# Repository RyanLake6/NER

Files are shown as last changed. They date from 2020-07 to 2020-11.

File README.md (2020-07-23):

View this project on [CADLAB.io](https://cadlab.io/project/23021). 

# NER
This is the GitHub repo for all code and schematics created for Northeastern's Electric Racing club.

- Electrical-Arduino: Arduino code for electrical subsystems, mainly the CAN Network
- Project Manangement: Javascript (Google Apps Script) code for various project management backend systems

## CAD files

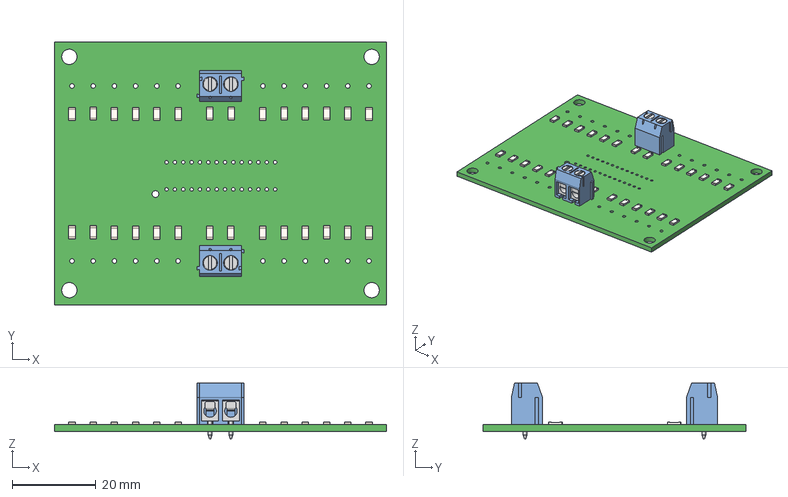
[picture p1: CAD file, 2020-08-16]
Schematics/Battery Managment/Therm_PCB/Therms.step
79.5 x 63.0 x 13.4 mm

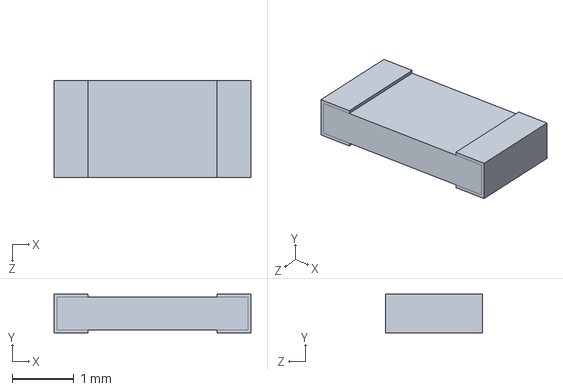
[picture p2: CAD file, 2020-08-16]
Schematics/Battery Managment/VoltTap_PCB/C1T5_CAD_Model.SLDPRT
3.20 x 0.63 x 1.58 mm

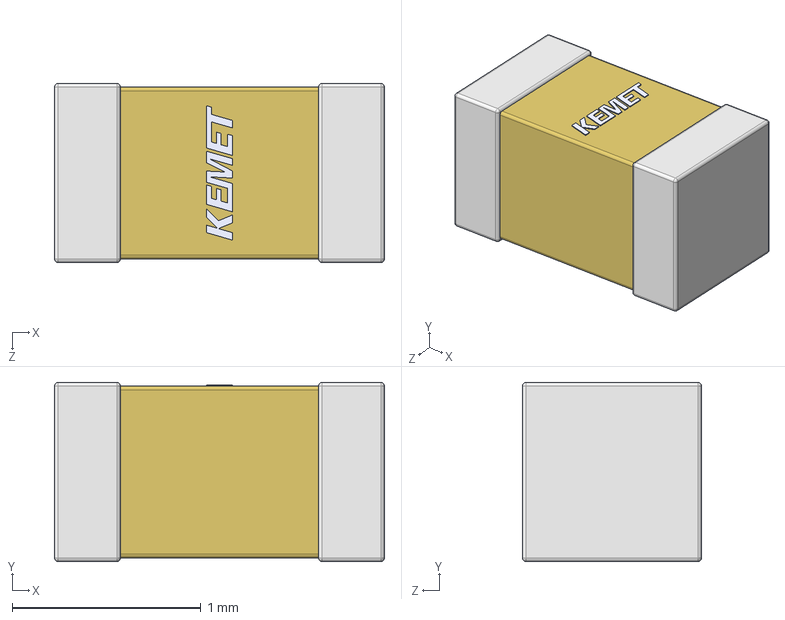
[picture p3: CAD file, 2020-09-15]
SchematicsAndPCBs/TSAL/TSALpowerboard/3dmodel/C0603C105K3RACTU.step
1.75 x 0.95 x 0.95 mm

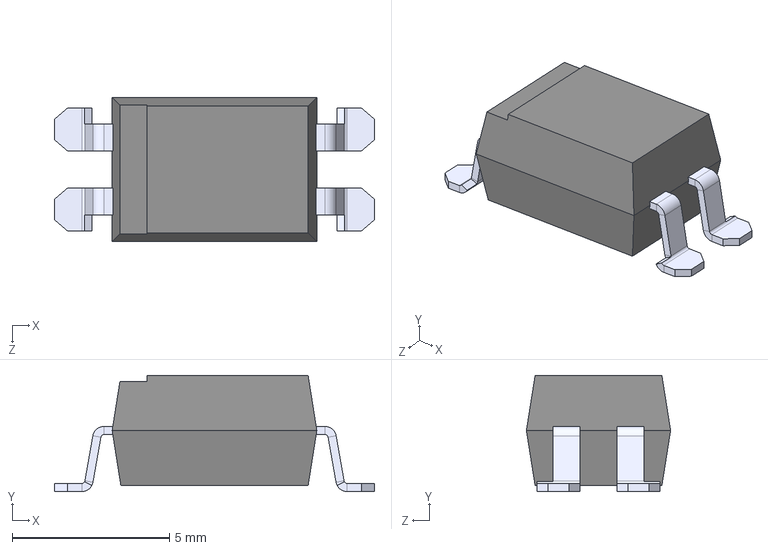
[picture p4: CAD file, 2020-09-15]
SchematicsAndPCBs/TSAL/TSALpowerboard/3dmodel/SFH617A.STEP
10.2 x 3.69 x 4.58 mm

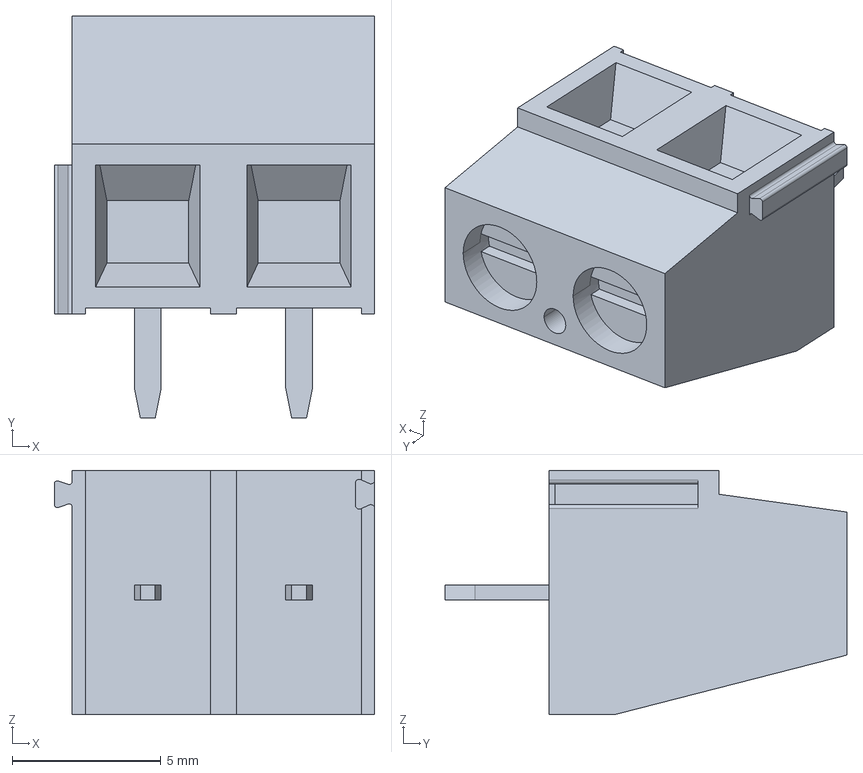
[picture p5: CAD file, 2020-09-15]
SchematicsAndPCBs/TSAL/TSALpowerboard/3dmodel/c-282837-2-g2-3d.stp
10.8 x 13.5 x 8.20 mm

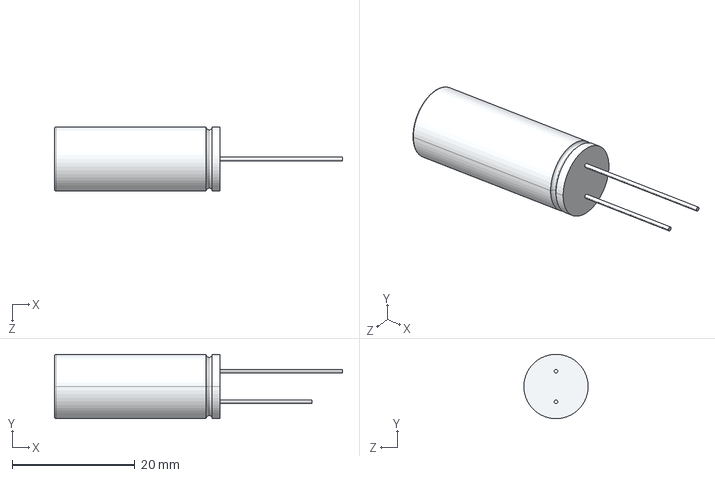
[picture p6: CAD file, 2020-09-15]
SchematicsAndPCBs/TSAL/TSALpowerboard/3dmodel/ESY827M025AH5AA.step
47.0 x 10.5 x 10.5 mm

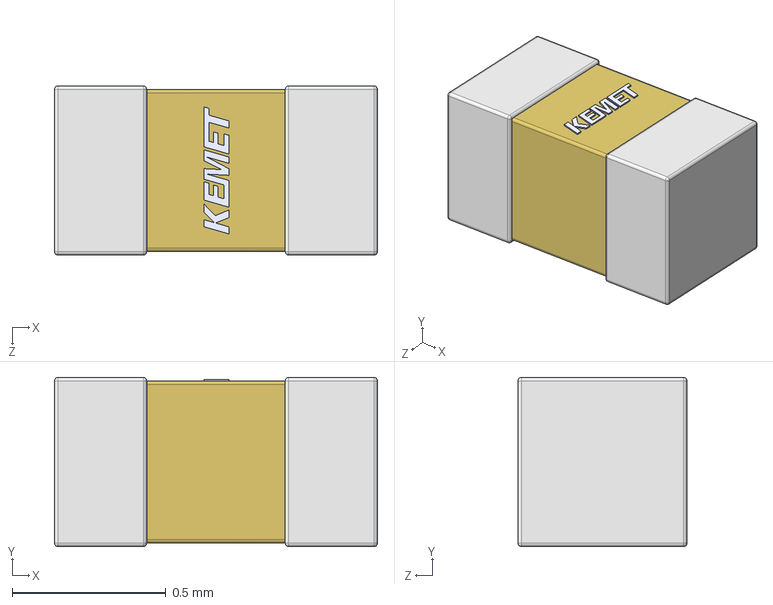
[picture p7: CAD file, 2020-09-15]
SchematicsAndPCBs/TSAL/TSALpowerboard/3dmodel/C0402C104K3RACTU.step
1.05 x 0.55 x 0.55 mm

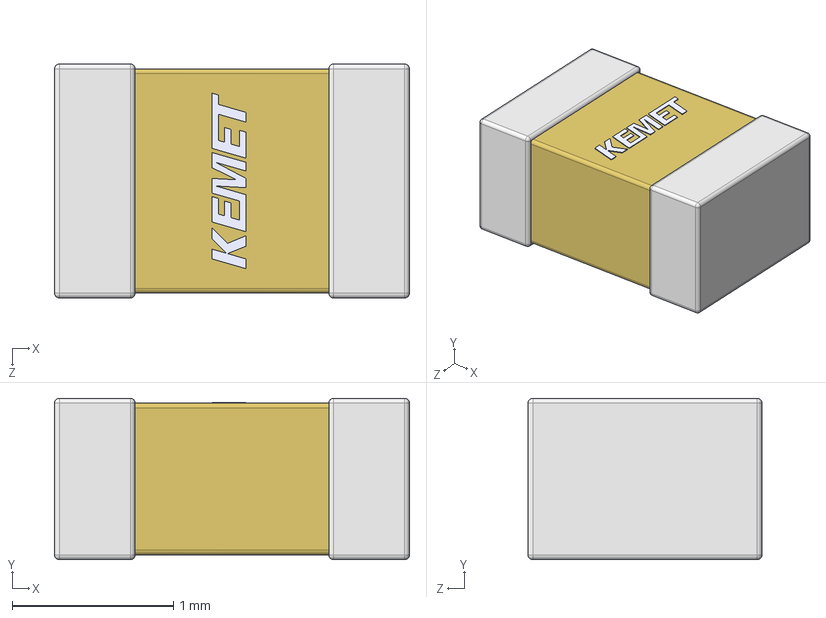
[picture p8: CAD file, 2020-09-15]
SchematicsAndPCBs/TSAL/TSALpowerboard/3dmodel/C0805C105K9PACTU.STEP
2.20 x 1.00 x 1.45 mm

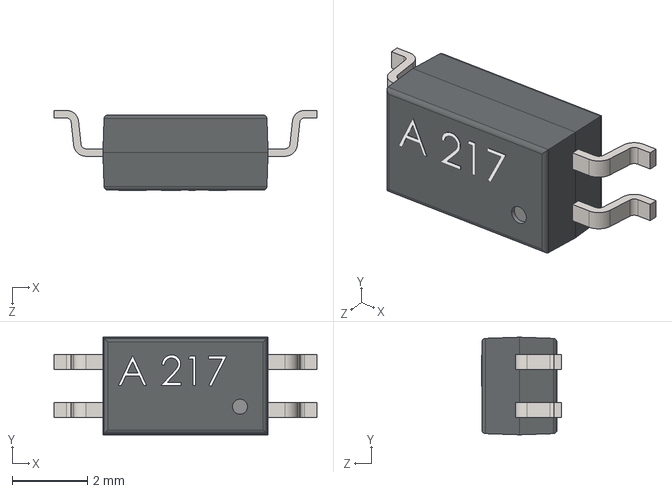
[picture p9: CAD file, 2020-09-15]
SchematicsAndPCBs/TSAL/TSALpowerboard/3dmodel/User Library-ACPL-217-56DE.STEP
7.00 x 2.60 x 2.13 mm

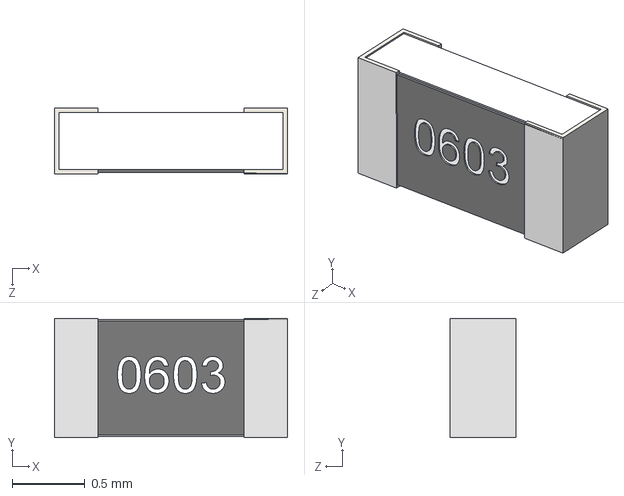
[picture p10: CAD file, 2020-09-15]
SchematicsAndPCBs/TSAL/TSALpowerboard/3dmodel/Library-Panasonic0603.STEP
1.60 x 0.82 x 0.45 mm

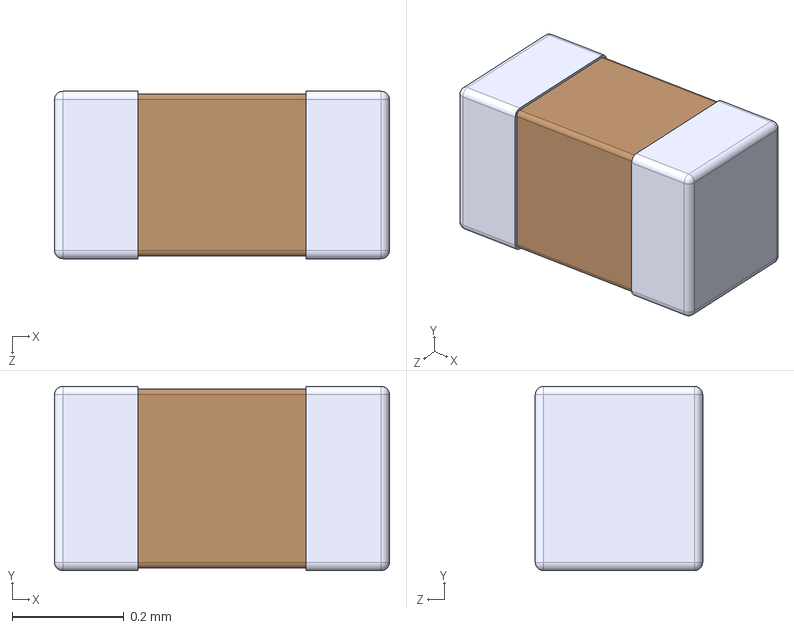
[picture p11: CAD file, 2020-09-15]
SchematicsAndPCBs/TSAL/TSALpowerboard/3dmodel/TMK063CG060FPGF.STEP
0.6 x 0.33 x 0.3 mm

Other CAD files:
Schematics/Battery Managment/VoltTap_PCB/Board.step.SLDASM
Schematics/Battery Managment/VoltTap_PCB/26.step.SLDPRT
Schematics/Battery Managment/VoltTap_PCB/6120xx21621_PIN.step.SLDPRT
Schematics/Battery Managment/VoltTap_PCB/C1T5_CAD_Model-0.step.SLDPRT
Schematics/Battery Managment/VoltTap_PCB/6120xx22021_LEVIER_COURT.step.SLDPRT
Schematics/Battery Managment/VoltTap_PCB/C1T5_CAD_Model.step.SLDPRT
Schematics/Battery Managment/VoltTap_PCB/C1T5_CAD_Model-1.step.SLDPRT
Schematics/Battery Managment/Therm_PCB/Therms.SLDPRT
Schematics/Battery Managment/VoltTap_PCB/6911027100xx_CAGE.step.SLDPRT
Schematics/Battery Managment/VoltTap_PCB/6911027100xx_PIN.step.SLDPRT
Schematics/Battery Managment/VoltTap_PCB/6911027100xx_VIS.step.SLDPRT
Schematics/Battery Managment/VoltTap_PCB/691502710002.step.SLDPRT
Schematics/OLD (Deprecated)/Battery Managment/Therm_PCB/Therms.SLDPRT
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

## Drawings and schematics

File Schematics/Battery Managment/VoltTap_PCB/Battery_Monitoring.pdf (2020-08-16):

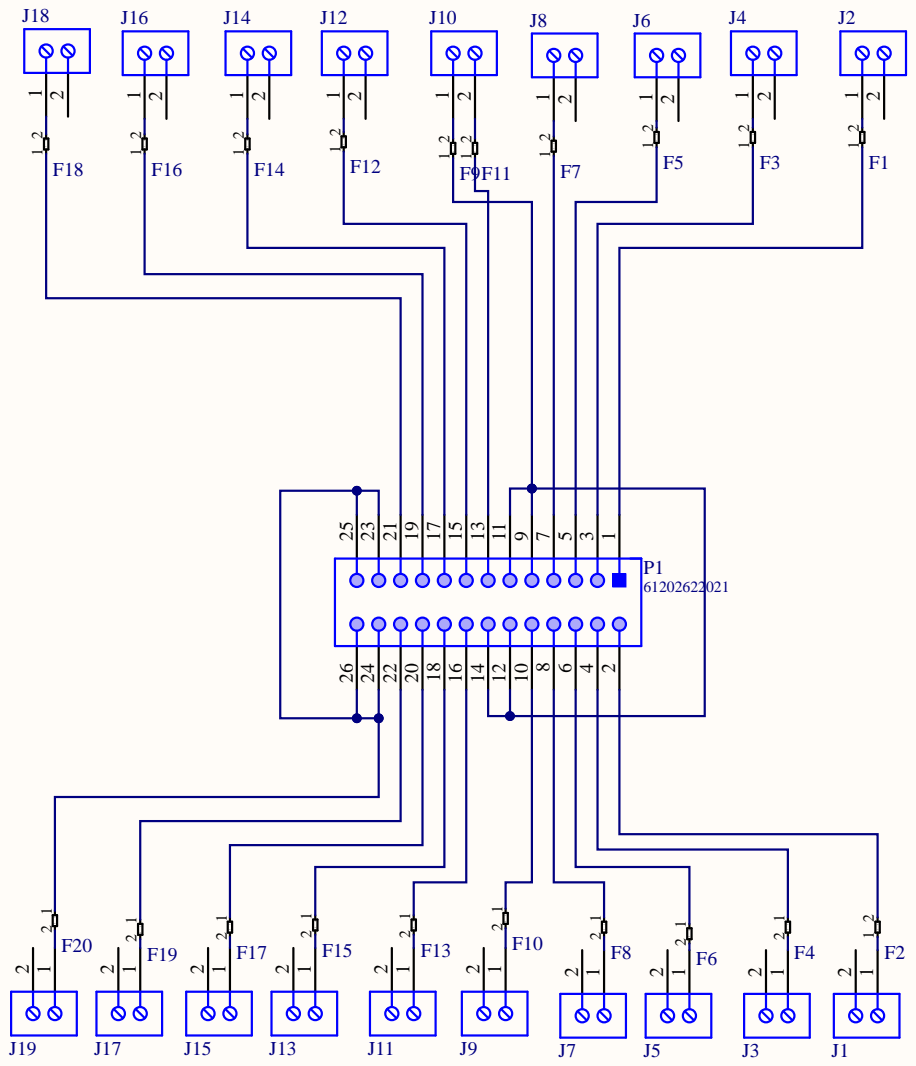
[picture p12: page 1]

Voltage Tap Fusing & Splitter
Title

Size: A | WBS: 2.2.1 | Revision: 1

Date: 8/15/2020 Time: 4:38:25 PM | | Sheet 1 of 1

Drawn By: Matthew McCauley

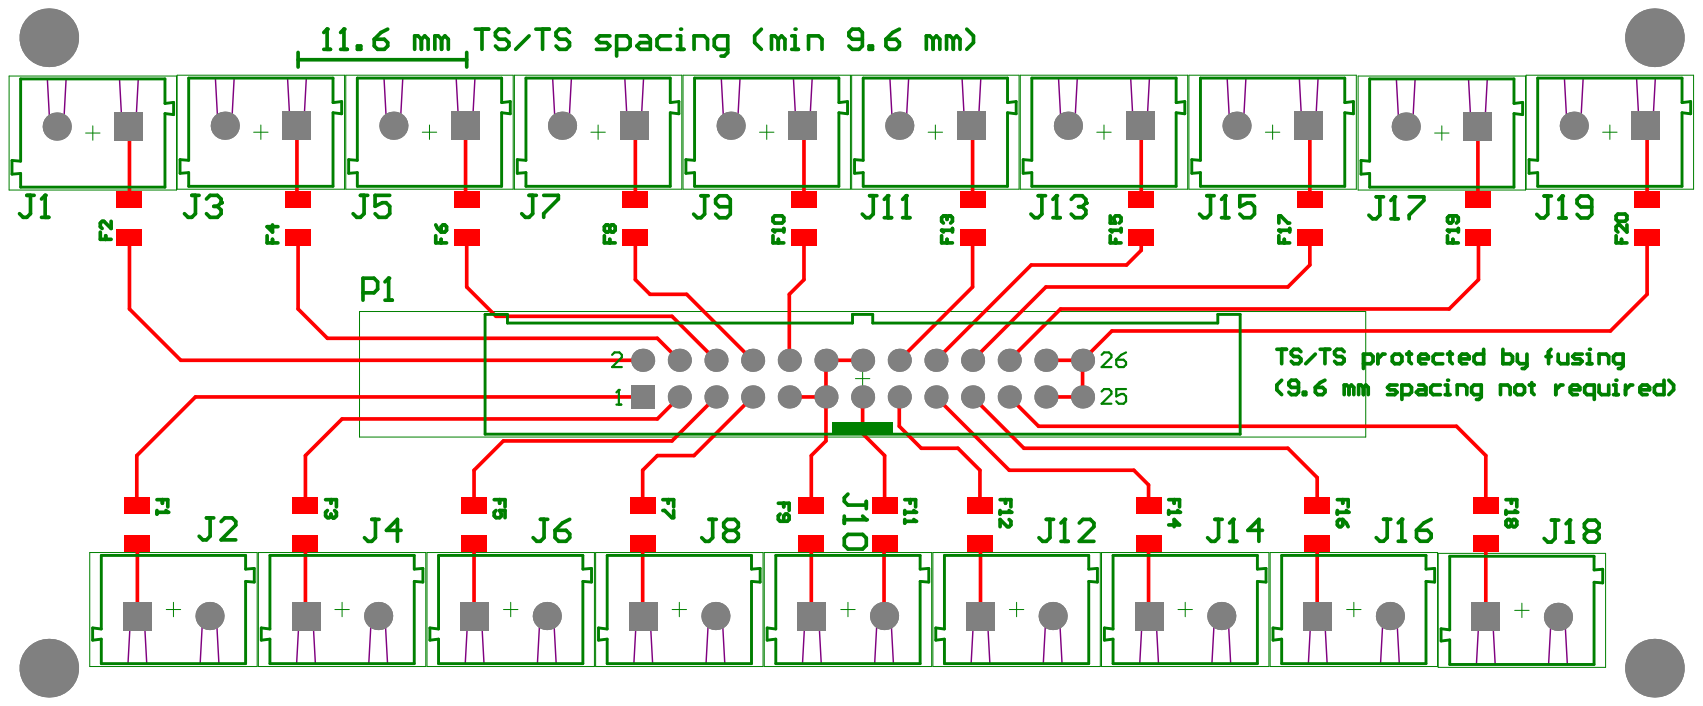
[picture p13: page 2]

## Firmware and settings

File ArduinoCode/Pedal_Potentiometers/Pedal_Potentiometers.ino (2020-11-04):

#include <mcp_can.h>
#include <mcp_can_dfs.h>
#include <SPI.h>

// potentiometer analog pins
int accelPin1 = A0; 
int accelPin2 = A1; 

// brake switch digital pins
int brakePin1 = 2;
int brakePin2 = 3;

// brake switch and potentiometer values
int accelPin1Val = 0; 
int accelPin2Val = 0;
int brakePin1Val;
int brakePin2Val;
 
// CAN stuff
const int CAN_ACCEL = 0x01;       // device's CAN id
const int CAN_ACCEL_BROKE = 0x02; // device error ID
const int CAN_BRAKE = 0x03;       // device's CAN id
const int CAN_BRAKE_BROKE = 0x04; // device error ID

//Dashboard variables
unsigned char len = 0;  //length of the data in the buffer
unsigned char buf[1];  //received data (only 1 byte)

const int SPI_CS_PIN = 10; // base CAN pin
unsigned char errorMessage[8] = {0, 255, 0, 0, 0, 0, 0, 0}; // output message for when the potentiometers are too far apart
// this message can be changed, but for now has value in second index as no "good" message will have a value there

MCP_CAN CAN(SPI_CS_PIN); // setup can device

/**
 * Start CAN and initialize digital pins
 */
void setup() {
  Serial.begin(115200); // baud rate for CAN

  while (CAN_OK != CAN.begin(CAN_500KBPS, MCP_8MHz)) { // specify 8MHz crystal
    Serial.println("CAN BUS init Failed"); // failure message
    delay(250); // delay, retry
  }
  Serial.println("CAN BUS Shield Init OK!"); // success message

  // Set brake light digital pins to act as inputs with built in pull-up resistors
  pinMode(brakePin1, INPUT_PULLUP);
  pinMode(brakePin2, INPUT_PULLUP);
}

/**
 * Continuoulsy read values of potentiometers and switches
 */
void loop() {
  readPotentiometers();
  readSwitches();
}

/**
 * Read the values of the two potentiometers
 * Compare them to make sure the values agree and send value to CAN
 */
void readPotentiometers() {
  accelPin1Val = analogRead(accelPin1); 
  accelPin2Val = analogRead(accelPin2);

  if (abs(accelPin1Val - accelPin2Val) <= (1024 * 0.1)) {
    int averageReading = (accelPin1Val + accelPin2Val) / 2;
    unsigned char byteReading = averageReading / 4;
    unsigned char valueMessage[8] = {byteReading, 0, 0, 0, 0, 0, 0, 0};
    CAN.sendMsgBuf(CAN_ACCEL, 0, 8, valueMessage); // send message of the average value of the two potentiometers
  } else {
    CAN.sendMsgBuf(CAN_ACCEL_BROKE, 0, 8, errorMessage); // send message that the two potentiometer values are too far apart
  }
}

/**
 * Read the values of the two switches
 * Compare them to make sure the values agree and send value to CAN
 */
void readSwitches() {
  brakePin1Val = digitalRead(brakePin1);
  brakePin2Val = digitalRead(brakePin2);

  if ((brakePin1Val == LOW) && (brakePin2Val == LOW)) {
    unsigned char valueMessage[8] = {1, 0, 0, 0, 0, 0, 0, 0};
    CAN.sendMsgBuf(CAN_BRAKE, 0, 8, valueMessage); // send message that the switches are turned on
  } else if (brakePin1Val != brakePin2Val) {
    CAN.sendMsgBuf(CAN_BRAKE_BROKE, 0, 8, errorMessage); // send message that the two switch values are not equal
  }
}

void readDashboard() {
    if(CAN_MSGAVAIL == CAN.checkReceive()) {   //if a new message has been recieved. 
      CAN.readMsgBuf(&len, buf); //enters message into program
      canId = CAN.getCanId(); //gets sender ID
     if (canID == 0x01) {  //determine whether Dashboard is on or off
      if (buf[0] == 0) {
       // code for when dashboad is off
      }
      else if (buf[0] == 1) {
       // code for when dashboard is on
      }
     }
     
     else if (canID == 0x02) {  //determine whether forward or revers
      if (buf[0] == 0) {
       // code for when in reverse
      }
      else if (buf[0] == 1) {
       // code for when forward
      }
     }
    }
}

void MsgMotorController(int torque, int direction, int inverter) {  //torque must be 0-255, direction 0 is reverse, 1 is forward, inverter 0 is off, 1 is on
 unsigned char valueMessage[8] = {torque, 0, 0, direction, inverter, 0, 0, 0};
 CAN.sendMsgBuf(CAN_MOTOR, 0, 8, valueMessage);
}

 

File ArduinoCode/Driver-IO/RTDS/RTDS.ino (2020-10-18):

// Author: Joshua Cheng
// Date: October 12, 2020

bool shutdownVoltage = false;
const int SHUTDOWN_DETECTION_PIN = 3; // Pin for detecting shutdown system voltage.
const int BUTTON_PIN = 2; // Pin for on/off button.
const int BUTTON_LED_PIN = 11; // Pin for integrated LED on the button.
const int SPEAKER_PIN = 10; // Pin for speaker or relay for speaker (must be pwm pin).
long speakerCooldown = 0;
long buttonCooldown = 0;
bool state = false;

/* 
 *  Sets relavent pins to output or input, initializes serial for debugging.
 */
void setup() {
  Serial.begin(115200);

  pinMode(SHUTDOWN_DETECTION_PIN, INPUT);
  pinMode(BUTTON_PIN, INPUT_PULLUP); // Uses built-in pullup resistor.

  pinMode(SPEAKER_PIN, OUTPUT);
  pinMode(BUTTON_LED_PIN, OUTPUT);
}

/** 
 *  On/off button with RTDS.
 *  
 *  Will only set vehicle to "ready to drive" if shutdown circuit is enabled and button is pressed.
 *  Button LED is activated when shutdown circuit is detected. Speaker will activate for 3 seconds when
 *  the vehicle becomes "ready to drive".
 */
void loop() {
  shutdownVoltage = digitalRead(SHUTDOWN_DETECTION_PIN); // Detects if shutdown circuit is active (5v divided from 12v). 

  // If shutdown circuit is active, turn on the LED. Otherwise, turn LED and speaker off, and set state to off
  if (shutdownVoltage) {
    digitalWrite(BUTTON_LED_PIN, HIGH);
  } else {
    digitalWrite(BUTTON_LED_PIN, LOW);
    state = 0;
    speakerCooldown = millis();
  }

  // Turns speaker off once cooldown is passed or state is false.
  if (speakerCooldown < millis() || !state) {
    // Serial.println("Speaker Off");
    analogWrite(SPEAKER_PIN, 0);
  }

  /* If the shutdown circuit is active, button cooldown has passed, and button is pressed,
   * toggle state, reset button cooldown. If state is true, turn on speaker.
   */
  if (shutdownVoltage && buttonCooldown < millis() && digitalRead(BUTTON_PIN) == LOW) {
    state = !state;
    buttonCooldown = millis() + 500; // Set cooldown to 500ms (prevents triggering button multiple times with one press).
    if (state) {
      analogWrite(SPEAKER_PIN, 128);
      // Serial.println("Speaker On");
      speakerCooldown = millis() + 3000;
    }
  }
  
  String s = "off";
  if (state) {
    s = "on";
  }
  Serial.println("STATE: " + s + "  |  Shutdown Circuit Detection: " + String(shutdownVoltage));
}

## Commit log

2020-08-16 Added Battery Managment PCBs
    -Added voltage tap schematic
    -Added thermistor schematic
    -Added voltage tap PCB
    -Added thermistor PCB
    [26.step.SLDPRT, 6120xx21621_PIN.step.SLDPRT, 6120xx22021_LEVIER_COURT.step.SLDPRT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]
2020-08-17 Replaced silkscreen with proper dimension
    [VoltTap.PcbDoc]
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2020-08-28 Master Schematic 1st revision
    Added Full battery, TS, Shutdown, and BMS and Motor Controller
    [Accumulator_Container.sch, BatterySegment1.sch, BatterySegment2.sch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]
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2020-09-06 Parts library System Updates
    >Added Kicad libraries folder to SchematicsandPCBs
    >Added NER parts library to KiCAD folder
    >Moved all custom parts to new NER library
    >Deleted old random libraries
    [Charger.sch, Full Battery System.sch]
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2020-09-15 Edited Shutdown Indicator wiring
    Added resistors for indicators, added gnd on driver i/o side
    [Shutdown.sch]
2020-09-15 Updating Library References
    Shifting references in the Master Schematic project to use the new NER library
    [Accumulator_Container.sch, BatterySegment1.sch, BatterySegment2.sch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]
2020-09-15 Added numbers and fixed library
    -Fixed custom parts to refer to NER lubrary
    -Added numbers to the new resistors and diodes
    [Shutdown.sch]
2020-09-17 Added new IMD fuse
    Needed both sense lines to be fused. Added F3 to represent this
    [Accumulator_Container.sch]
2020-09-17 Paper Size and Title Blocks
    -Switched all paper sizes over to America units (letter size A and tabloid size B) (so we can actually be cool and print them an stuff)
    -Fixed title blocks to use sheet properties
    -Started some changes to the accumulator segment schematic
    [Accumulator_Container.sch, BatterySegment.sch, BatterySegment3.sch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]
2020-09-17 Officially retiring individual projects
    The Master Schematic Project has supersceded the individual schematics. All changes should now be made to the main schematic project
    [394250002.stp, 395021003.stp, 430450412.stp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]
2020-09-17 Therms and Volt Taps
    Mostly fixed all thermistor and volt taps
    Also created new sheet for BMS container and updated library part for OrionThermExpansionModule
    [Accumulator_Container.sch, BMSContainer.sch, BatterySegment.sch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]
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2020-09-18 Fixed Driver IO sheet
    Added driver io enclosure sheet
    [Accumulator_Container.sch, BMSContainer.sch, BatterySegment.sch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]
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2020-09-18 Added GLV Fusebox component
    Made fusebox component, and added to master schematic
    [Accumulator_Container.sch, BMSContainer.sch, BatterySegment.sch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]
2020-09-18 General cleanup, and fixes
    >Shutdown latch circuits updated
    >Shutdown latch resets updated
    >BMS cleaned up
    >Some wire runs cleaned up
    [Master System Schematic.sch, Shutdown_LatchingCircuits.sch]
2020-09-18 Additional Updates/Cleanup
    >Removed unessescary project file (Shutdown circuit project file - not needed as a hierarchical sheet)
    >Moved a couple wires
    [Master System Schematic.sch, Shutdown_System.sch]
2020-09-20 Fixed symbol library issues
    >Migrated 3polerelay to NER and replaced in schematic
    >Used built in Diode instead of custom diode
    [Shutdown_LatchingCircuits.sch]
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2020-09-20 Cleanup and general fixes
    >Added TSAL circuit sheet
    >Added project files for each sheet (kicad makes them automatically so might as well have them for editing indivudual sheets)
    >Cleaned up wire runs
    >Added LED as stand in for TSAL
    [Accumulator_Container.sch, BMSContainer.sch, BatterySegment.sch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]
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2020-09-23 Adding ground pin to fault pcb enclosure
    Needed ground pin for fault pcb enclosure
    [Master System Schematic.sch, Shutdown_LatchingCircuits.sch]
2020-09-24 Updated shutdown circuit to reflect changes
    >updated latching circuit design to be 4 DPDT relays
    >updated reset switch design to be dpst button to actuate both latches simultaneously
    [Master System Schematic.sch, Shutdown_LatchingCircuits.sch]
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2020-09-24 Fixed a weird duplicate onto master
    [Accumulator_Container.sch, BMSContainer.sch, BatterySegment.sch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]
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2020-09-24 Component IDs
    Assigned remaining missing numbers
    [Accumulator_Container.sch]
2020-09-25 integrated matts Battery BOx updates
    added MC air control lines
    Moved tsal to after imd fuse
    [Accumulator_Container.sch, BMSContainer.sch, BatterySegment.sch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]
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2020-09-25 Wire run updates, prettying up
    >Moved SMDs and HVDs outside of accumulator container for consistency (all human activated switches and indicators should be in top level sheet)
    >minor wire run updates and cleanup in accumulator container
    >minor wire run cleanup in master schematic
    [Accumulator_Container.sch, Master System Schematic.sch]
2020-10-03 Connectors and Start of Numbering
    Created new generic connectors and applied numbering tool to whole project
    [Accumulator_Container.sch, BMSContainer.sch, BatterySegment.sch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]
2020-10-03 Resolved number conflicts
    [BatterySegment.sch, Master System Schematic.sch]
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2020-10-07 Revert "Driver IO Update"
    This reverts commit 719adb322f5430e89ce6e16a8f4347f22c153558.
    [Accumulator_Container.sch, BMSContainer.sch, BatterySegment.sch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]
2020-10-11 New Relay Module Symbol/ Some Parts Added to Driver IO Container
    (Note: Make sure to check that I didn't make some catastrophically horrible changes to everything by accident)
    [Accumulator_Container.sch, BMSContainer.sch, BatterySegment.sch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]
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2020-10-12 Finished IO Container, Added Brake Light
    In the IO Container: made connections between Speaker, Arduino, CAN, Relay Module, and Button. Made new symbol for the Button.
    In Master Schematic: added Brake Light Container.
    In Brake Light Container: made connections between CAN, Relay Module, and Arduino. Still missing LED (but that will be in Master Schematic.)
    [Accumulator_Container.sch, BMSContainer.sch, BatterySegment.sch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]
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2020-10-12 Moved BMS Current Sensor
    Moved current sensor to be inside the accumulator container, as it physically will be
    [Accumulator_Container.sch, BMSContainer.sch, BatterySegment.sch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]
2020-10-12 Fixed Connection to BMS
    [Accumulator_Container.sch, BMSContainer.sch, Master System Schematic.sch]
2020-10-12 Added CAN Bus
    Added CAN bus to master schematic and fixed pin positions as needed to keep it clean
    [BMSContainer.sch, Master System Schematic.sch]
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2020-10-12 Added Brake LED Symbol and Finished Brake Light Sheet
    Final Julius draft of Brake Light and IO sheets before I get Cam to check if my connections are all true.
    [Brake Light.sch, Master System Schematic.sch]
2020-10-12 Updated issue date
    [Accumulator_Container.sch, BMSContainer.sch, BatterySegment.sch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]
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2020-10-13 Fixed Master
    Readded all the things lost in the merge on master.
    [Accumulator_Container.sch, BMSContainer.sch, BatterySegment.sch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]
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2020-10-14 Cooling Pump, TSMP container Updates
    >Added Cooling pump relay
    >Added Cooling pump
    >Added +12V plug to TSMP container
    [Accumulator_Container.sch, BMSContainer.sch, BatterySegment.sch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]
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2020-10-14 Wire Runs and cleanup
    >Cleaned up some wire runs
    >Added Charger safety connection
    [BMSContainer.sch, Master System Schematic.sch]
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2020-10-15 Fixed Typo
    Just cleaning up before sending a copy to rules committee
    [Accumulator_Container.sch]
2020-10-15 Updated TSAL
    Updated TSAL to now also tap from inside the AIRs
    [Accumulator_Container.sch, TSAL_Circuit.sch]
2020-10-15 Removed Pull Down Resistors
    Removed based on the fact that the microprocessor has built in pull up resistors
    [PedalBox.sch]
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2020-10-15 Fixed Broken Library References
    [Accumulator_Container.sch, BMSContainer.sch, BatterySegment.sch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]
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2020-10-15 StartEnable w/ Voltage Divider
    Added StartEnable wire to the dashboard can box and added a voltage divider with proper resistors to bring voltage down from 12V to 5V.
    [Driver IO Enclosure.sch, Master System Schematic.sch]
2020-10-15 Fixed Pin and Updated Title Block
    -Fixed incorrectly imported pin
    -Actually wired the pin in the master schematic
    -Updated title block
    [Accumulator_Container.sch, BMSContainer.sch, BatterySegment.sch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]
2020-10-16 Created Voltage tap PCBs
    >Made tap pcbs, not connected
    >placeholder for thermistor pcb
    [Accumulator_Container.sch, BMSContainer.sch, BatterySegment.sch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]
2020-10-16 Further fixing merge
    [Accumulator_Container.sch, BMSContainer.sch, BatterySegment.sch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]
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2020-10-16 BMS Schematic Edits 1
    Added BMS2V2 component
    Updated Thermistor Expansion
    Cleaned up BMSContainer schematic
    [BMSContainer.sch]
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2020-10-16 FINISHED Voltage tap PCB schem
    >reran battery box to fit new schem
    >added placeholder thermistor board schem.
    [Accumulator_Container.sch, BMSContainer.sch, BatterySegment.sch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]
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2020-10-16 Fixed CAN
    Changed to represent one connection. This ofc can be changed back if you meant to imply two CAN connections coming in
    [Accumulator_Container.sch, BMSContainer.sch, BatterySegment.sch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]
2020-10-16 Revert "Merge branch 'ZackBMSEdits' of https://github.com/Northeastern-Electric-Racing/NER into ZackBMSEdits"
    This reverts commit cc098d90d0538ae4a07a8875f467bf325998b3da, reversing
    changes made to 1b52e21c70c5d0f94c162de68c3d3b766612d1c9.
    [Accumulator_Container.sch, BMSContainer.sch, BatterySegment.sch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]
2020-10-16 Final cleanup
    Fixed some no-connects
    Annotated
    Added revision number and title information
    [BMSContainer.sch]
2020-10-16 Additional corrections
    >Moved GLV+ and GLV_GND pins to indicate single connections to enclosure
    >Added charger safety line to charger
    [Accumulator_Container.sch, BMSContainer.sch, BatterySegment.sch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]
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2020-10-16 Revert "Zack BMS Edits"
    [Accumulator_Container.sch, BMSContainer.sch, BatterySegment.sch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]
2020-10-16 FIXED IT MANUALLY
    [BMSContainer.sch, BatterySegment.sch, Brake Light.sch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]
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2020-10-16 Fixed Driver IO and annotations
    [Accumulator_Container.sch, BMSContainer.sch, BatterySegment.sch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]
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2020-10-18 Fixed an overlapping wire
    [Accumulator_Container.sch, BMSContainer.sch, BatterySegment.sch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]
2020-10-18 Fixed Arduino wiring
    [Driver IO Enclosure.sch]
2020-10-18 Fixed Driver IO LED Voltage Divider
    Added voltage divider to LED to bring 5v down to 3v.
    [Accumulator_Container.sch, BMSContainer.sch, BatterySegment.sch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]
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2020-10-19 Fixed Wiring on CAN Bus
    I fixed the wiring on the CAN Bus in the brake light box that I messed up yesterday.
    [Brake Light.sch]
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2020-10-23 Fixed BMSContainer component
    Added 2 connectors and fixed wiring
    Updated annotations
    Updated version
    [BMSContainer.sch]
2020-10-23 Fixed name of BMS2
    [BMSContainer.sch]
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2020-10-23 Fixed Segment tap wiring
    [Accumulator_Container.sch, BMSContainer.sch, BatterySegment.sch]
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2020-10-25 Updated 12V charger connection
    Fixed 12v hookup to use only one connector
    [Master System Schematic.sch, ThermistorPCB.sch, VT_PCB.sch]
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2020-10-26 Fixed cooling pump shutoff
    >replaced with extra relay
    [Master System Schematic.sch]
2020-10-26 Fixed issues from merge fix
    [BMSContainer.sch, BatterySegment.sch, Master System Schematic.sch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]
2020-10-26 fixed another loose wire
    [Master System Schematic.sch]
2020-10-26 Fixed annotations and date
    [Accumulator_Container.sch, BMSContainer.sch, BatterySegment.sch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]
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2020-10-28 Fixed BMS Charge Power Relay
    wasnt implemented properly before
    [BMSContainer.sch]
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2020-10-29 Fixed Issues from last update
    Sent the toggle - to the 5v, made connections between BMS/IMD Fault (formerly just called indicator) pins and the BMD/IMD + pins
    [Accumulator_Container.sch, BMSContainer.sch, BatterySegment.sch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]
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
